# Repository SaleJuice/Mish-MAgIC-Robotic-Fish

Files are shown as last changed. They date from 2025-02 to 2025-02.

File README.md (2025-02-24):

# Mish: MAgIC Robotic Fish

## Introduction

**Mish** is a three joints robotic fish prototype, mimiced a typical carangiform fish with Body and/or Caudal Fin (BCF) propulsion mode, enabling agile planar movement near the water surface. A key feature distinguishing  **Mish** from others is its capability to provide real-time joint position feedback, enhancing state representations for the controller, which is beneficial for generating multi-model swimming policy based on learning-based method, such as end-to-end Reinforcement Learning (RL).



This repository aims to provide comprehensive details of **Mish**, facilitating the creation of similar models by enthusiasts. We hope **Mish** can contribute to the development of the robotic fish community and support related scientific research work. 

If you have any questions, please feel free to raise an ISSUE. I am happy to help you reproduce your own **Mish**.

## Demonstration

**Mish** currently supports wireless control of the desired angle position of joints through UDP protocol at a maximum frequency of 50Hz. Before running the python script in upper computer, please ensure that the **Mish** and the upper computer are on the same WIFI network and check if the IP address and port are correct.

By running the ```demonstration.py``` script, it can be observed that the robotic fish swings its joints with sine signal.

<div align="center">
  <video width="640" height="" controls>
    <source src="" type="video/mp4">
  </video>
</div>

## Production

**Mish**'s dimensions are 0.52m * 0.13m * 0.12 m, weighing 1.1 kg. The prototype is comprised of three main components: (i) a rigid head housing an MCU board with the ESP32-S3 module and an 800 mAh 7.4 V lithium battery; (ii) a deformable body consisting of three joints connected by aluminum components and covered with rubber skin; and (iii) a rigid tail.

<div align="center">
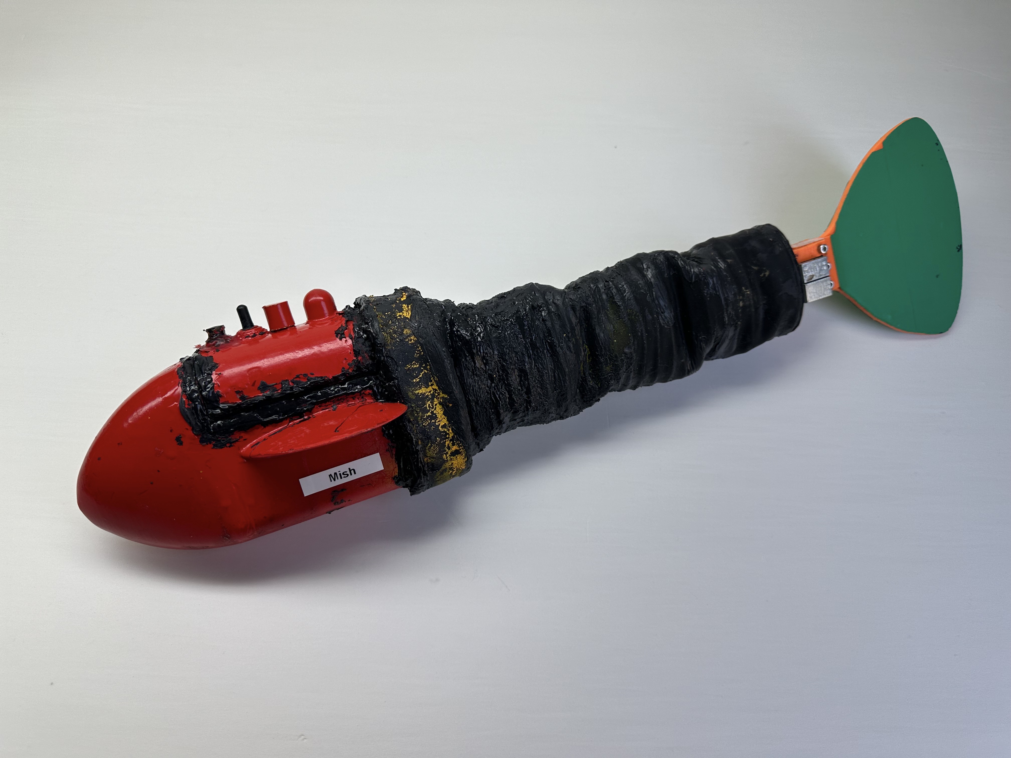
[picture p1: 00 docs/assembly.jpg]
  
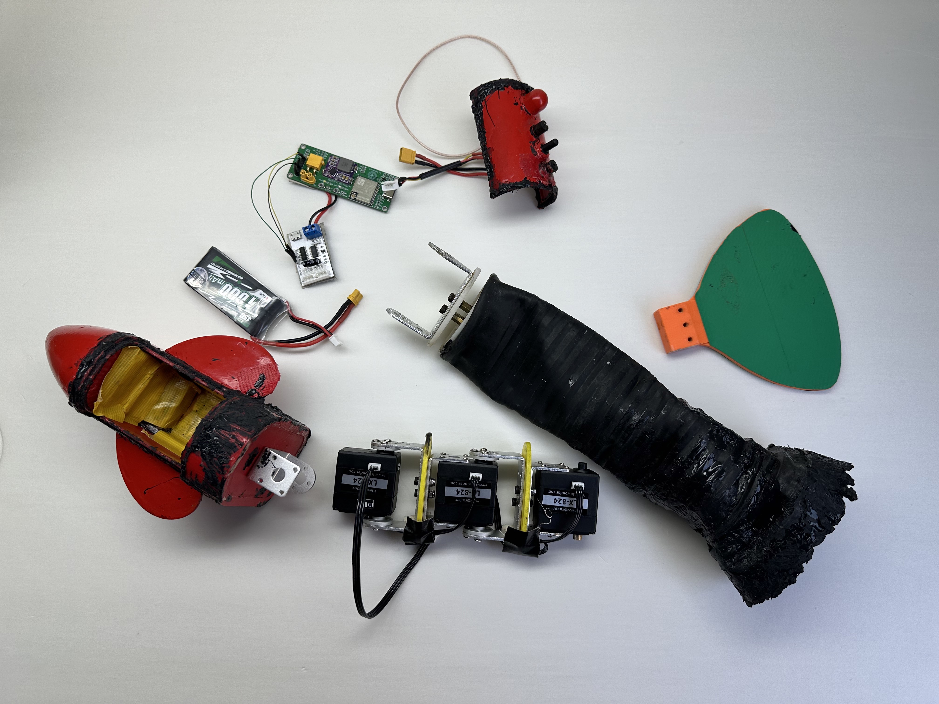
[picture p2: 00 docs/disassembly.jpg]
  
</div>

The head and tail are 3D-printed from ABS plastic (PLA is even better) and coated with epoxy resin for waterproofing. Each joint is driven by a Hiwonder LX-824 servomotor with a maximum torque of 17 kg*cm, a no-load speed of 0.2 second per 60 degree. The density of the prototype is adjusted slightly lower than water to focus on its planar motion.

All the production materials for **Mish** have been provided, please refer to [docs](./00%20docs/), [model](./01%20model/), [hardware](./02%20hardware/) and [firmware](./03%20firmware/) for more details.

## Acknowledgment

The author is very grateful for the help of Yangyang Zhao, Hongru Dai, Xu Huang and Yuhang Zhao from the [MAgIC Lab](https://magiclab.sist.shanghaitech.edu.cn) at [ShanghaiTech Univeristy](https://www.shanghaitech.edu.cn/eng/).

## References

0. [Learning Agile Swimming: An End-to-End Approach Without CPGs](https://arxiv.org/abs/2409.10019)
1. [CPG-Based Locomotion Control Of A Robotic Fish: Using Linear Oscillators And Reducing Control Parameters Via PSO](http://www.ijicic.org/10-05048-1.pdf)
2. [Bottom-Level Motion Control For Robotic Fish To Swim In Groups: Modeling And Experiments](https://iopscience.iop.org/article/10.1088/1748-3190/ab1052)
3. [A General CPG Network And Its Implementation On The Microcontroller](https://www.sciencedirect.com/science/article/abs/pii/S0925231215005354)

## BibTeX

If you think this repository is helpful to you, please consider citing our latest work.

```bash
@article{lin2025learning,
  title={Learning Agile Swimming: An End-to-End Approach Without CPGs},
  author={Lin, Xiaozhu and Liu, Xiaopei and Wang, Yang},
  journal={IEEE Robotics and Automation Letters},
  year={2025},
  publisher={IEEE}
}
```

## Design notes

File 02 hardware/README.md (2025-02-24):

# Hardware

LCEDA-Pro: https://oshwhub.com/linxzh/magic-fish

The R14 position can be shorted by soldering or by soldering a 0 ohm resistor. The C11 capacitor at the boot position does not need to be soldered, otherwise there may be a situation where pressing reset is necessary to operate.

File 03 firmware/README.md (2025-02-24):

# Firmware

In this project, we use Arduino IDE to upload the firmware code to the main control board. For details about installation of Arduino IDE and configuration and upload of ESP32 boards, please refer to [Espressif Official Arduino-ESP32 Documents](https://docs.espressif.com/projects/arduino-esp32/en/latest/index.html).

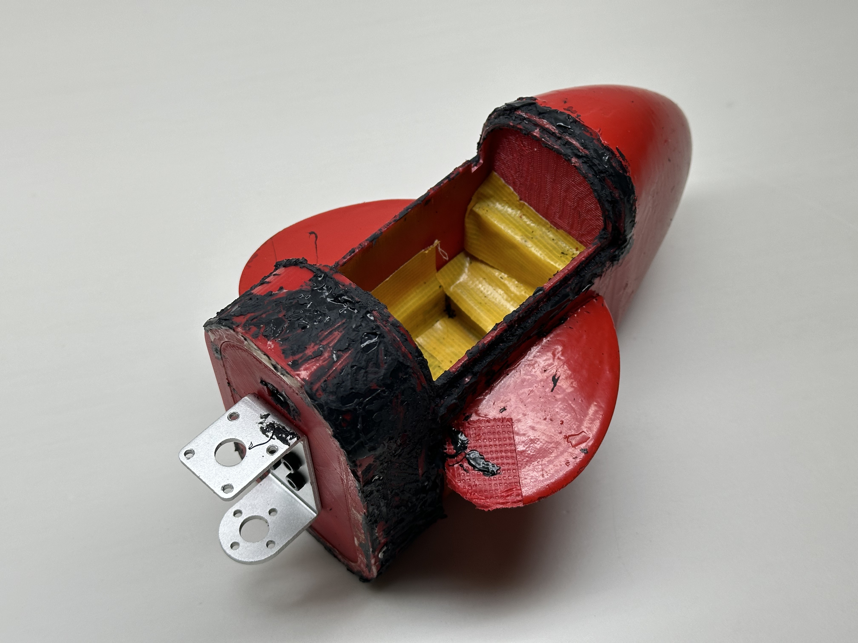
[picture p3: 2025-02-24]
00 docs/head_back.jpg

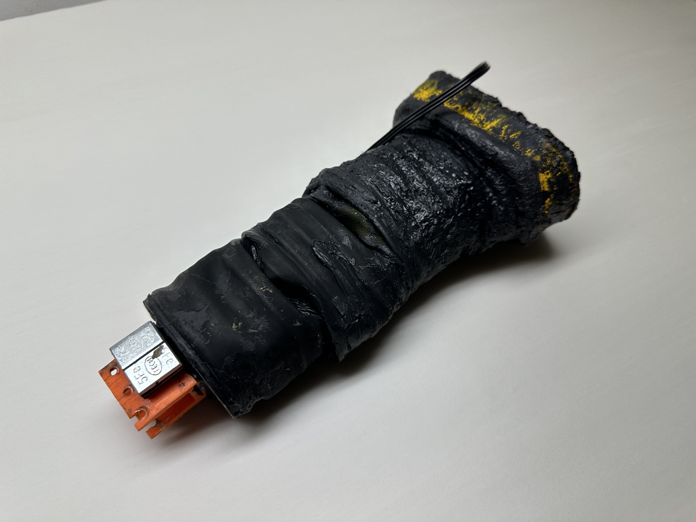
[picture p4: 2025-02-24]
00 docs/body_with_skin_2.jpg

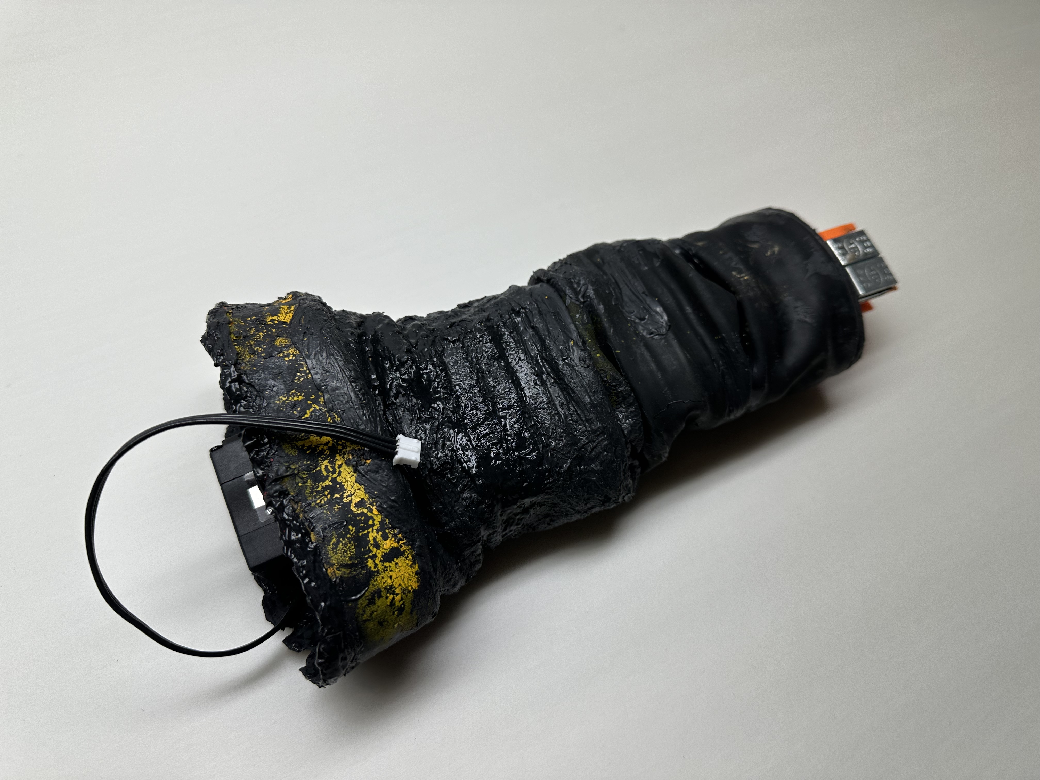
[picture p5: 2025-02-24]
00 docs/body_with_skin_1.jpg

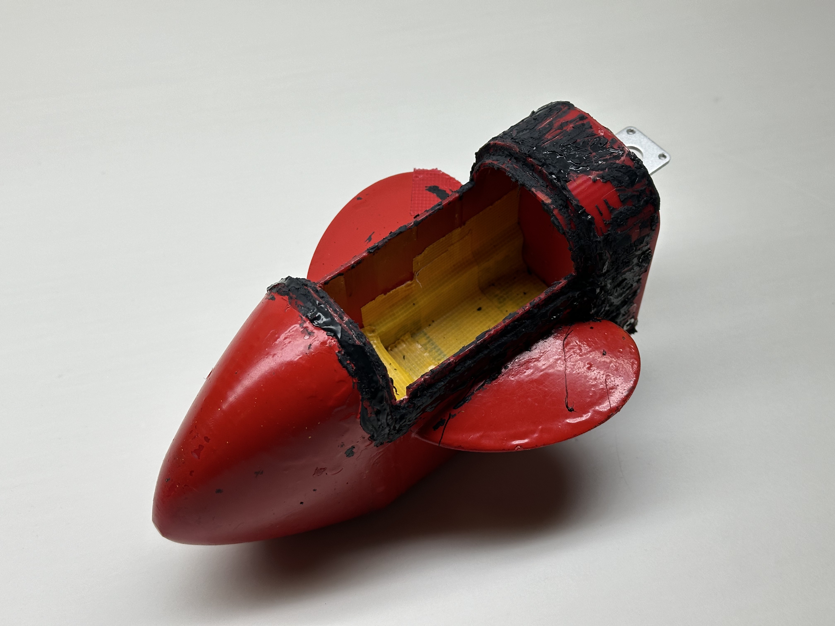
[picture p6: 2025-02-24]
00 docs/head_front.jpg

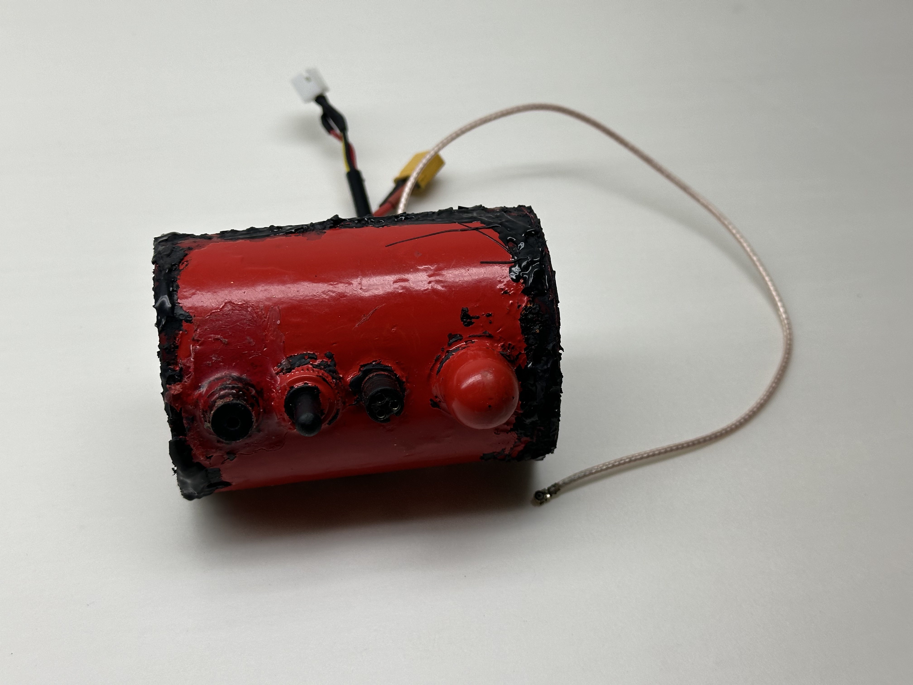
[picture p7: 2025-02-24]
00 docs/cover_with_all_outside.jpg

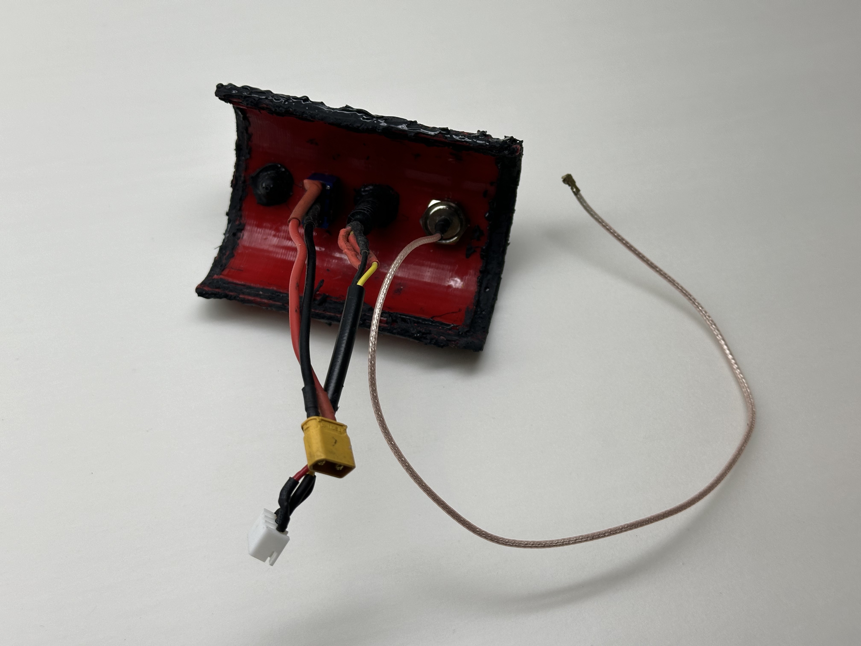
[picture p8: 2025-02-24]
00 docs/cover_with_all_inside.jpg

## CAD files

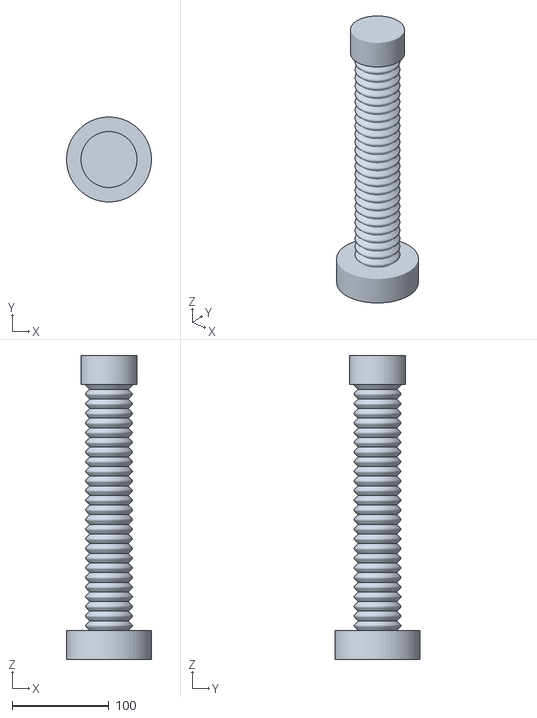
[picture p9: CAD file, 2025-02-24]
01 model/fish_skin_mold.stl
88.0 x 88.0 x 315.0

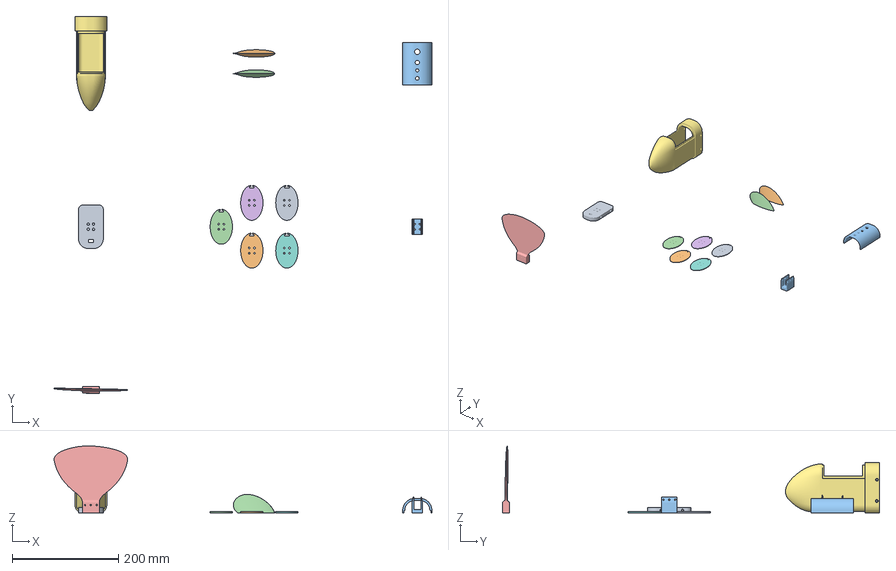
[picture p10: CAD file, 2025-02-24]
01 model/mish.3mf
711.2 x 709.6 x 126.1 mm
鱼骨支撑.stl x 5
鱼鳍.stl x 2
鱼尾夹板.stl
鱼尾.stl
鱼头仓.stl
鱼头后盖.stl
鱼头上盖.stl

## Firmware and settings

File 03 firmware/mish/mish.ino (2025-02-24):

/*
  Description: This is the firmware code for the robotic fish 'Mish'.
  Date: 2025-02-18 20:31:31
  Creator: Xiaozhu Lin (linxzh@shanghaitech.edu.cn)
  Last Modification Date: 2025-02-23 16:57:33
  Last Editors: Xiaozhu Lin (linxzh@shanghaitech.edu.cn)
  Version: 0.1.0
*/


#include <Arduino.h>

#include <math.h>
#include <Ticker.h>
#include <WiFi.h>

#include <AsyncUDP.h>

#include <ESPmDNS.h>
#include <WiFiUdp.h>
#include <ArduinoOTA.h>

#include "LobotSerialServo.h"


const float rad2deg = 180 / PI;
const float deg2rad = PI / 180;

const float deg2bit = 1000 / 240;
const float bit2deg = 240 / 1000;

const float rad2bit = rad2deg * deg2bit;
const float bit2rad = bit2deg * deg2rad;


const gpio_num_t led_pin = GPIO_NUM_21;
float led_value = 0;

const gpio_num_t servo_tx_pin = GPIO_NUM_4;
const gpio_num_t servo_rx_pin = GPIO_NUM_5;
const int servo_nums = 3;
typedef struct
{
  int id;
  int position;
  int central_position;
  int vin;
  int temp;
  int alive;
} servo_info_t;
servo_info_t servo_info[servo_nums] = {{1, 0, 510, 0, 0, true}, {2, 0, 520, 0, 0, true}, {3, 0, 510, 0, 0, true}};

typedef struct
{
  float theta[servo_nums];
  float speed[servo_nums];
} downward_info_t;
downward_info_t downward_info = {{0.0, 0.0, 0.0}, {0.0, 0.0, 0.0}};

typedef struct
{
  int id[servo_nums];
  float theta[servo_nums];  // rad \in [-1.047, 1.047]
  float vin[servo_nums];
  int temp[servo_nums];
} upward_info_t;
upward_info_t upward_info = {{0, 0, 0}, {0.0, 0.0, 0.0}, {0.0, 0.0, 0.0}, {0, 0, 0}};

const char *ssid = "MAgIC_Fish_Project";
const char *password = "123456789";

AsyncUDP UdpSocket;
unsigned int local_port = 2333;
unsigned int remote_port = 6060;
IPAddress remote_ip(192, 168, 1, 101);

Ticker upward_timer;


void setup()
{
  Serial.begin(115200);

  pinMode(led_pin, OUTPUT);
  pinMode(beep_pin, OUTPUT);

  Serial1.begin(115200, SERIAL_8N1, servo_rx_pin, servo_tx_pin);
  
  Serial.println();
  Serial.print("[SERVO] ID: ");
  for (int i = 0; i < servo_nums; i++)
  {
    servo_info[i].alive = LobotSerialServoReadLoadOrUnload(Serial1, servo_info[i].id) >= 0;
    if (servo_info[i].alive)  // for read function stuck avoid
    {
      Serial.print(servo_info[i].id);
      Serial.print(", ");
    }
  }
  Serial.println("is ALIVE!");
  delay(1000);

  for (int i = 0; i < servo_nums; i++)
  {
    LobotSerialServoMove(Serial1, servo_info[i].id, servo_info[i].central_position, 1000);
  }
  
  WiFi.mode(WIFI_STA);
  WiFi.begin(ssid, password);
  Serial.print("[WIFI] Connecting to: ");
  Serial.println(ssid);
  while (!WiFi.isConnected())
  {
    delay(1000);  // ms
    Serial.print(".");
  }
  Serial.println("");
  Serial.print("[WIFI] IP is: ");
  Serial.println(WiFi.localIP());
  delay(3000);

  while (!UdpSocket.listen(local_port));
  UdpSocket.onPacket(downward_callback_func);

  upward_timer.attach_ms(20, upward_timing_func);

  ArduinoOTA.begin();  // NOT DELETE IT
}

void loop()
{
  ArduinoOTA.handle();  // NOT DELETE IT

  // int servo_index = 0, set_position = 0;

  // adjust the central value of the servomotor through serial input
  // if(Serial.available() > 0)
  // {
  //   int value = Serial.parseInt();
  //   servo_info[servo_index].central_position = value;
  //   Serial.readStringUntil('\n');
  // }
  // LobotSerialServoMove(Serial1, servo_info[servo_index].id, servo_info[servo_index].central_position, 0);
  
  // generate sine periodic signal to check the working status of the servomotor
  // set_position = sin(2 * PI * millis() / 1000) * 100 + 500;
  // LobotSerialServoMove(Serial1, servo_info[servo_index].id, set_position, 0);

  // Serial.print("set_position:");
  // Serial.print(set_position);
  // Serial.print(", ");
  
  // Serial.print("servo_info[");
  // Serial.print(servo_index);
  // Serial.print("].central_position:");
  // Serial.print(servo_info[servo_index].central_position);
  // Serial.print(", ");
  
  // Serial.print("servo_info[");
  // Serial.print(servo_index);
  // Serial.print("].position:");
  // Serial.print(servo_info[servo_index].position);
  // Serial.print(", ");
  
  // Serial.print("servo_info[");
  // Serial.print(servo_index);
  // Serial.print("].vin:");
  // Serial.print(servo_info[servo_index].vin);
  // Serial.print(", ");
  
  // Serial.print("servo_info[");
  // Serial.print(servo_index);
  // Serial.print("].temp:");
  // Serial.print(servo_info[servo_index].temp);
  // Serial.println();
  
  // delay(20);
}

void upward_timing_func()
{
  digitalWrite(led_pin, LOW);
  
  for (int i = 0; i < servo_nums; i++)  // cost 2.5ms * 3
  {
    if (servo_info[i].alive)
    {
      servo_info[i].position = LobotSerialServoReadPosition(Serial1, servo_info[i].id);
    }
  }
  
  if (servo_info[0].alive)
  {
    servo_info[0].vin = LobotSerialServoReadVin(Serial1, servo_info[0].id);  // cost 2.5ms
  }
  servo_info[1].vin = servo_info[0].vin;
  servo_info[2].vin = servo_info[0].vin;

  if (servo_info[0].alive)
  {
    servo_info[0].temp = LobotSerialServoReadTemp(Serial1, servo_info[0].id);  // cost 2.5ms
  }
  servo_info[1].temp = servo_info[0].temp;
  servo_info[2].temp = servo_info[0].temp;

  for (int i = 0; i < servo_nums; i++)
  {
    upward_info.id[i] = servo_info[i].id;
    upward_info.theta[i] = (servo_info[i].position - servo_info[i].central_position) * bit2rad;  // rad
    upward_info.vin[i] = servo_info[i].vin / 1000.0;
    upward_info.temp[i] = servo_info[i].temp;
  }

  uint8_t packet[sizeof(upward_info_t)];
  memcpy(packet, &upward_info, sizeof(packet));

  UdpSocket.connect(remote_ip, remote_port);
  UdpSocket.write(packet, sizeof(upward_info_t));
  UdpSocket.close();

  digitalWrite(led_pin, HIGH);
}

void downward_callback_func(AsyncUDPPacket packet)
{
  digitalWrite(led_pin, LOW);

  memcpy(&downward_info, packet.data(), sizeof(downward_info));
  
  for (int i = 0; i < servo_nums; i++)  // servo control
  {
    downward_info.theta[i] = fclamp(downward_info.theta[i], -1.047, 1.047);  // rad
    int desired_position = round(servo_info[i].central_position + downward_info.theta[i] * rad2bit);  // bit
    
    int cost_time;
    if (downward_info.speed[i] > 0)  // ATTENTION !!!
    {
      downward_info.speed[i] = fclamp(downward_info.speed[i], 0.05, 5.23);  // rad/s
      int current_theta = (servo_info[i].position - servo_info[i].central_position) * bit2rad;  // rad
      cost_time = abs(round((current_theta - downward_info.theta[i]) * 1000.0 / downward_info.speed[i]));  // ms
    }
    else
    {
      cost_time = 0;  // ms
    }
    LobotSerialServoMove(Serial1, servo_info[i].id, desired_position, cost_time);
  }

  digitalWrite(led_pin, HIGH);
}


float fclamp(float val, float O_Min, float O_Max) {
  return min(max(val, O_Min), O_Max);
}

float fmap(float val, float I_Min, float I_Max, float O_Min, float O_Max) {
  return (((val - I_Min) * ((O_Max - O_Min) / (I_Max - I_Min))) + O_Min);
}

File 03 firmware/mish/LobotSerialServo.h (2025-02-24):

#define GET_LOW_BYTE(A) (uint8_t)((A))
//宏函数 获得A的低八位
#define GET_HIGH_BYTE(A) (uint8_t)((A) >> 8)
//宏函数 获得A的高八位
#define BYTE_TO_HW(A, B) ((((uint16_t)(A)) << 8) | (uint8_t)(B))
//宏函数 以A为高八位 B为低八位 合并为16位整形

#define ID_ALL 254  //ID为254时，会向所有舵机进行广播，可用于读取未知ID的舵机信息

#define LOBOT_SERVO_FRAME_HEADER         0x55
#define LOBOT_SERVO_MOVE_TIME_WRITE      1
#define LOBOT_SERVO_MOVE_TIME_READ       2
#define LOBOT_SERVO_MOVE_TIME_WAIT_WRITE 7
#define LOBOT_SERVO_MOVE_TIME_WAIT_READ  8
#define LOBOT_SERVO_MOVE_START           11
#define LOBOT_SERVO_MOVE_STOP            12
#define LOBOT_SERVO_ID_WRITE             13
#define LOBOT_SERVO_ID_READ              14
#define LOBOT_SERVO_ANGLE_OFFSET_ADJUST  17
#define LOBOT_SERVO_ANGLE_OFFSET_WRITE   18
#define LOBOT_SERVO_ANGLE_OFFSET_READ    19
#define LOBOT_SERVO_ANGLE_LIMIT_WRITE    20
#define LOBOT_SERVO_ANGLE_LIMIT_READ     21
#define LOBOT_SERVO_VIN_LIMIT_WRITE      22
#define LOBOT_SERVO_VIN_LIMIT_READ       23
#define LOBOT_SERVO_TEMP_MAX_LIMIT_WRITE 24
#define LOBOT_SERVO_TEMP_MAX_LIMIT_READ  25
#define LOBOT_SERVO_TEMP_READ            26
#define LOBOT_SERVO_VIN_READ             27
#define LOBOT_SERVO_POS_READ             28
#define LOBOT_SERVO_OR_MOTOR_MODE_WRITE  29
#define LOBOT_SERVO_OR_MOTOR_MODE_READ   30
#define LOBOT_SERVO_LOAD_OR_UNLOAD_WRITE 31
#define LOBOT_SERVO_LOAD_OR_UNLOAD_READ  32
#define LOBOT_SERVO_LED_CTRL_WRITE       33
#define LOBOT_SERVO_LED_CTRL_READ        34
#define LOBOT_SERVO_LED_ERROR_WRITE      35
#define LOBOT_SERVO_LED_ERROR_READ       36


//校验和
byte LobotCheckSum(byte buf[])
{
  byte i;
  uint16_t temp = 0;
  for (i = 2; i < buf[3] + 2; i++) {
    temp += buf[i];
  }
  temp = ~temp;
  i = (byte)temp;
  return i;
}

int LobotSerialServoReceiveHandle(HardwareSerial &SerialX, byte *ret)
{
  bool frameStarted = false;
  bool receiveFinished = false;
  byte frameCount = 0;
  byte dataCount = 0;
  byte dataLength = 2;
  byte rxBuf;
  byte recvBuf[32];
  byte i;

  unsigned long startTime = millis();
  while (millis() - startTime < 1000)
  {
    if (SerialX.available() > 0)
    {
      rxBuf = SerialX.read();
      
      if (!frameStarted)
      {      
        if (rxBuf == LOBOT_SERVO_FRAME_HEADER)
        {
          frameCount++;
          if (frameCount == 2)
          {
            frameCount = 0;
            frameStarted = true;
            dataCount = 1;
          }
        }
        else
        {
          frameStarted = false;
          dataCount = 0;
          frameCount = 0;
        }
      }

      if (frameStarted)
      {
        recvBuf[dataCount] = (uint8_t)rxBuf;
        if (dataCount == 3)
        {
          dataLength = recvBuf[dataCount];
          if (dataLength < 3 || dataCount > 7)
          {
            dataLength = 2;
            frameStarted = false;
          }
        }
        dataCount++;
        if (dataCount == dataLength + 3)
        {
          if (LobotCheckSum(recvBuf) == recvBuf[dataCount - 1])
          {
            frameStarted = false;
            memcpy(ret, recvBuf + 4, dataLength);
            return 1;
          }
          return -1;
        }
      }
    }
  }
  
  return -2;
}

// //解析接收到的数据包信息，并返回
// int LobotSerialServoReceiveHandle(HardwareSerial &SerialX, byte *ret)
// {
//   bool frameStarted = false;
//   bool receiveFinished = false;
//   byte frameCount = 0;
//   byte dataCount = 0;
//   byte dataLength = 2;
//   byte rxBuf;
//   byte recvBuf[32];
//   byte i;

//   // delayMicroseconds(100);  // add 2025/02/19 by linxzh


//   while (SerialX.available())
//   {
//     rxBuf = SerialX.read();
//     // delayMicroseconds(100);
    
//     if (!frameStarted)
//     {      
//       if (rxBuf == LOBOT_SERVO_FRAME_HEADER)
//       {
//         frameCount++;
//         if (frameCount == 2)
//         {
//           frameCount = 0;
//           frameStarted = true;
//           dataCount = 1;
//         }
//       }
//       else
//       {
//         frameStarted = false;
//         dataCount = 0;
//         frameCount = 0;
//       }
//     }

//     if (frameStarted)
//     {
//       recvBuf[dataCount] = (uint8_t)rxBuf;
//       if (dataCount == 3)
//       {
//         dataLength = recvBuf[dataCount];
//         if (dataLength < 3 || dataCount > 7)
//         {
//           dataLength = 2;
//           frameStarted = false;
//         }
//       }
//       dataCount++;
//       if (dataCount == dataLength + 3)
//       {
//         if (LobotCheckSum(recvBuf) == recvBuf[dataCount - 1])
//         {
//           frameStarted = false;
//           memcpy(ret, recvBuf + 4, dataLength);
//           return 1;
//         }
//         return -1;
//       }
//     }
//   }
//   return -2;
// }

//写入舵机ID
void LobotSerialServoSetID(HardwareSerial &SerialX, uint8_t oldID, uint8_t newID)
{
  byte buf[7];
  buf[0] = buf[1] = LOBOT_SERVO_FRAME_HEADER;
  buf[2] = oldID;
  buf[3] = 4;
  buf[4] = LOBOT_SERVO_ID_WRITE;
  buf[5] = newID;
  buf[6] = LobotCheckSum(buf);
  SerialX.write(buf, 7);
}

//控制舵机转动
void LobotSerialServoMove(HardwareSerial &SerialX, uint8_t id, int16_t position, uint16_t time)
{
  byte buf[10];
  if(position < 0)
    position = 0;
  if(position > 1000)
    position = 1000;
  buf[0] = buf[1] = LOBOT_SERVO_FRAME_HEADER;
  buf[2] = id;
  buf[3] = 7;
  buf[4] = LOBOT_SERVO_MOVE_TIME_WRITE;
  buf[5] = GET_LOW_BYTE(position);
  buf[6] = GET_HIGH_BYTE(position);
  buf[7] = GET_LOW_BYTE(time);
  buf[8] = GET_HIGH_BYTE(time);
  buf[9] = LobotCheckSum(buf);
  SerialX.write(buf, 10);
}

//读取ID
int LobotSerialServoReadID(HardwareSerial &SerialX)
{
  int count = 10000;
  int ret;
  byte buf[6];
  
  buf[0] = buf[1] = LOBOT_SERVO_FRAME_HEADER;
  buf[2] = ID_ALL;  //ID_ALL为254，表示向所有舵机进行广播，可用于读取未知ID的舵机信息
  buf[3] = 3;
  buf[4] = LOBOT_SERVO_ID_READ;
  buf[5] = LobotCheckSum(buf);
  SerialX.write(buf, 6);

  
  while (SerialX.available())
    SerialX.read();

  while (!SerialX.available()) {
    count -= 1;
    if (count < 0)
      return -2048;
  }

  if (LobotSerialServoReceiveHandle(SerialX, buf) > 0)
    ret = (int16_t)BYTE_TO_HW(0x00, buf[1]);
  else
    ret = -2048;
  return ret;
}

//读取舵机位置
int LobotSerialServoReadPosition(HardwareSerial &SerialX, uint8_t id)
{
  int count = 10000;
  int ret;
  byte buf[6];

  buf[0] = buf[1] = LOBOT_SERVO_FRAME_HEADER;
  buf[2] = id;
  buf[3] = 3;
  buf[4] = LOBOT_SERVO_POS_READ;
  buf[5] = LobotCheckSum(buf);
  SerialX.write(buf, 6);
  
  while (SerialX.available())
    SerialX.read();

  while (!SerialX.available()) {
    count -= 1;
    if (count < 0)
      return -1;
  }

  if (LobotSerialServoReceiveHandle(SerialX, buf) > 0)
    ret = (int16_t)BYTE_TO_HW(buf[2], buf[1]);
  else
    ret = -2048;
  return ret;
}
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
